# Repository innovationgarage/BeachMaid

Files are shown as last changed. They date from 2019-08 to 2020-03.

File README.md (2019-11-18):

# ePiMP
Electric Powered Intelligent Multipurpose Platform



In short, the ePiMP is a low cost, open source wooden tank robot, that can be constructed by a single sheet of 12 mm plywood, two cheap battery powered drills and few 3d printed parts.

## Changelog

* 2019-09-16: Version 1.1
   - Handles and holes to the backcover
   - Battery measurement circuit
   - Replaced wooden drive gears by plastic ones
   - 2 new mounting holes in the "lip" parts
* 2019-06-31: First version

## Fabrication

### Wooden pieces
All the pieces fit in a standard 2.44m by 1.2m sheet of plywood, 12 mm (15/32 in) thickness. The thickness can be changed but that would require changes in some internal slots that interlock, and some plastic pieces that assume 12 mm as the thickness.

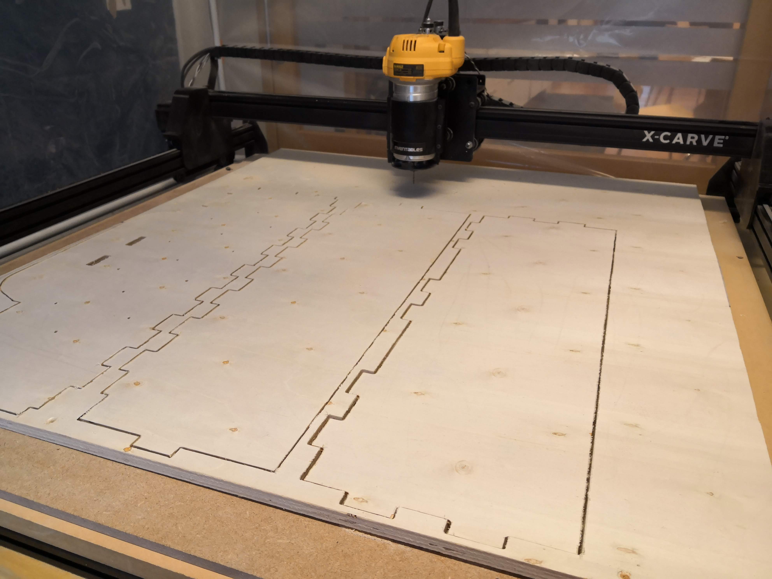
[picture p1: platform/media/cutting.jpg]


The list of parts wooden parts to cut in the CNC is aprox. 112 total pieces (depending on the version of the design)

#### Already layout sheets (for X-Carve 1000mm or similar)

The layout use 790mm square sheets:

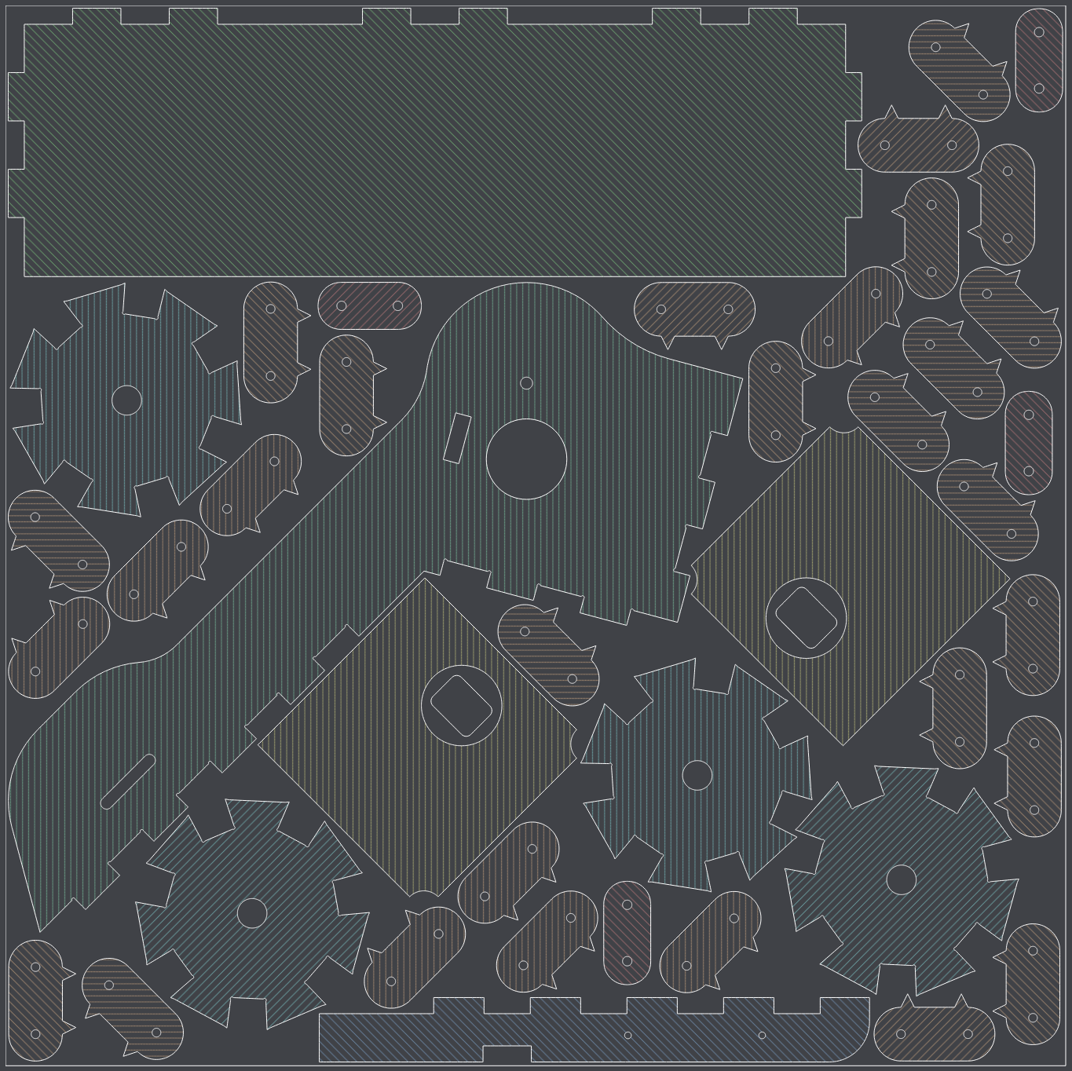
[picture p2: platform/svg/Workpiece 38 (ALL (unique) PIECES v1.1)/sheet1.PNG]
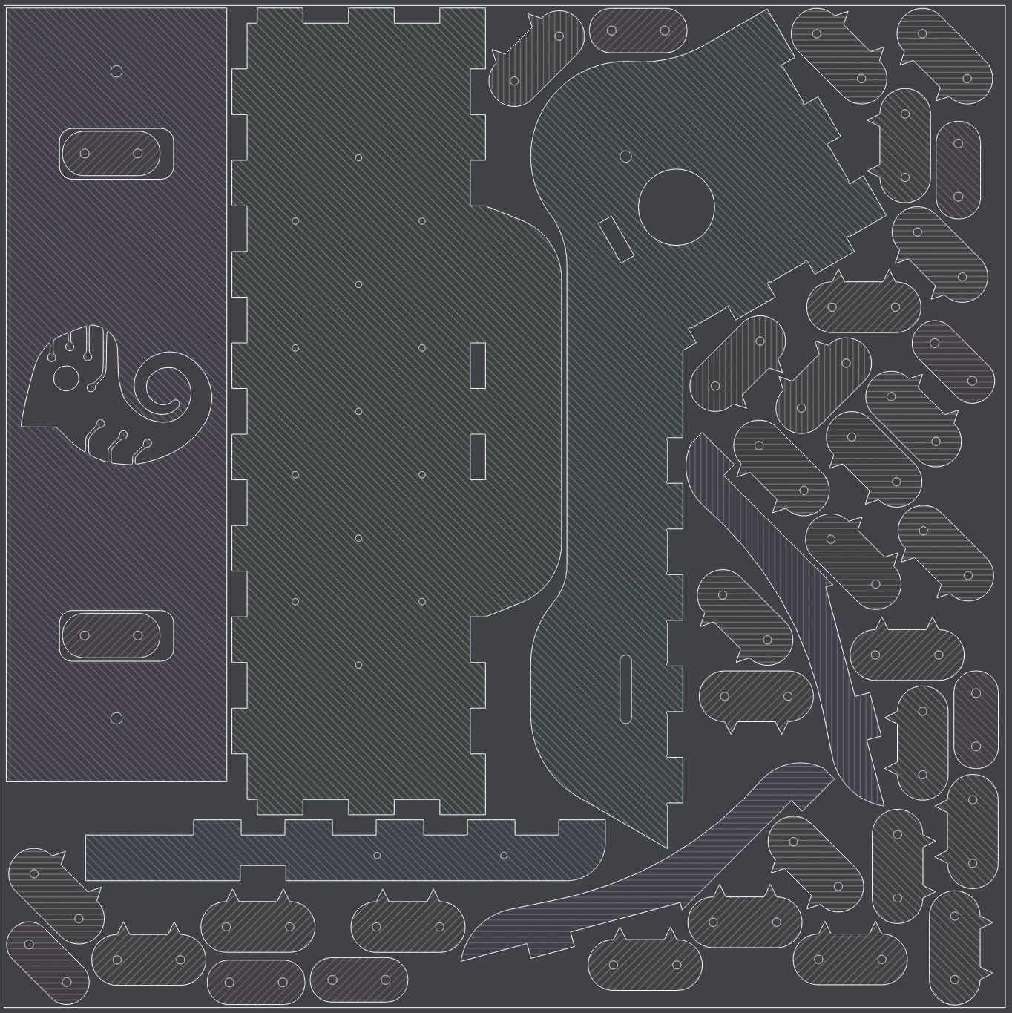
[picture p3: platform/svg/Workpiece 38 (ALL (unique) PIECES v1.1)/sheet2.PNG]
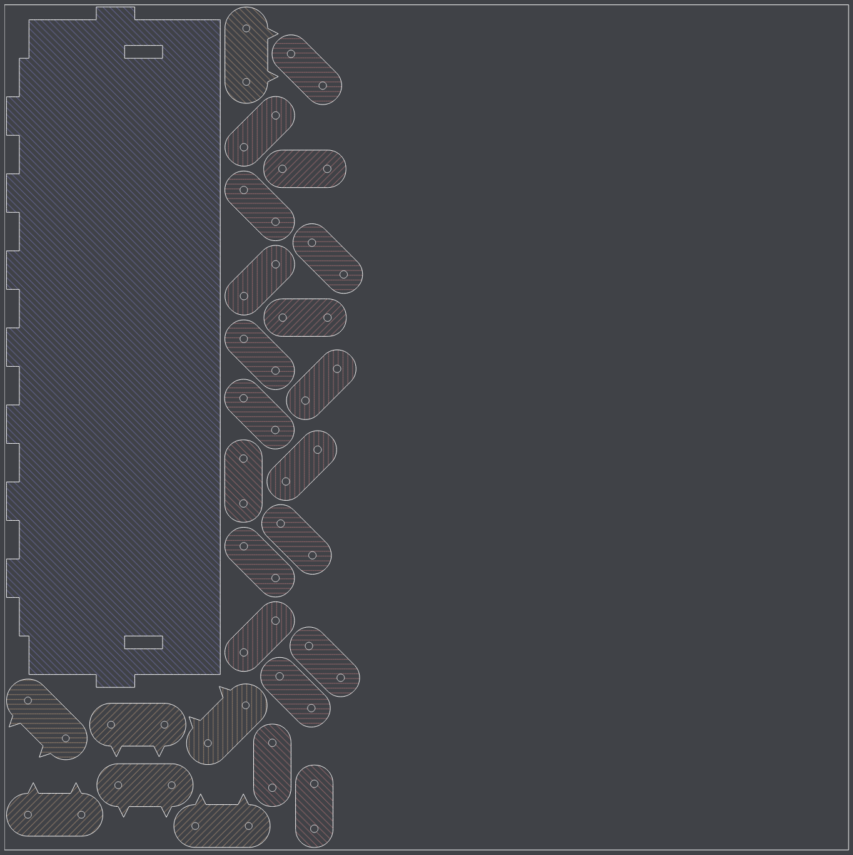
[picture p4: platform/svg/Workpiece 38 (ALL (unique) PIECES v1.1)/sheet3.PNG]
  

https://github.com/innovationgarage/epimp-body/blob/master/platform/svg/Workpiece%2038%20(ALL%20(unique)%20PIECES%20v1.1)/nested_optimized3.svg

#### Unique pieces

https://github.com/innovationgarage/epimp-body/blob/master/platform/svg/Workpiece%2038%20(ALL%20(unique)%20PIECES%20v1.1)/design.svg

The required quantity of the pieces is:

![](platform/svg/Workpiece%2038%20(ALL%20(unique)%20PIECES%20v1.1)/quantity.PNG)

### Plastic pieces
The list of needed printed parts is (56 total pieces, by the quantity specified in the filename):
https://github.com/innovationgarage/epimp-body/tree/master/platform/stl

## Assembly
You need the following parts and tools for the assembly:
* Wood glue
* Screwdrivers and wrenches
* 4x M8 long bolts (>10 cm) for the wheels
* 6x M8 inserts
* 2x M8 short bolts (>4 cm) for the back cover
* 2x M6 bolts and nut set for the clutch holder for the drills
* 2x cheap drills https://www.biltema.no/verktoy/el-verktoy/boremaskiner/drillskrutrekker-cd-12v-2000028475
* 8x skateboard ball bearings (608Z)
* 28x M6, 15 mm wood screws for the wheel center part that holds the bearings
* M5, 12 mm wood screws 
* M8 washers

### Wooden body

### Tank tracks
The tank tracks require 64x 6mm thick by 40 mm length wooden dowels https://www.aliexpress.com/item/32908209214.html. Before cutting the link pieces, test the fit of your dowels to ensure the friction between the outer parts is enough to hold everything without glue.

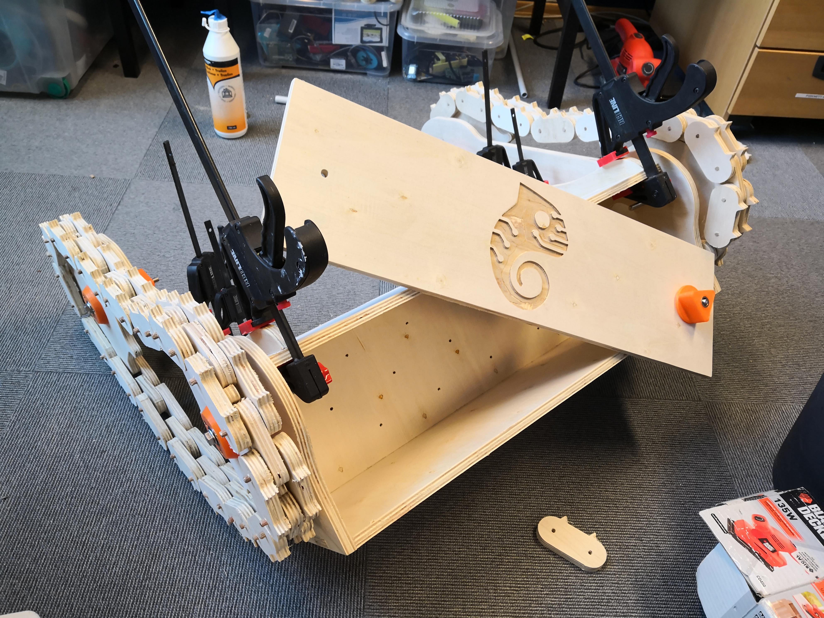
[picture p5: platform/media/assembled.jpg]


### Wheels and gears
The assembly is the following:

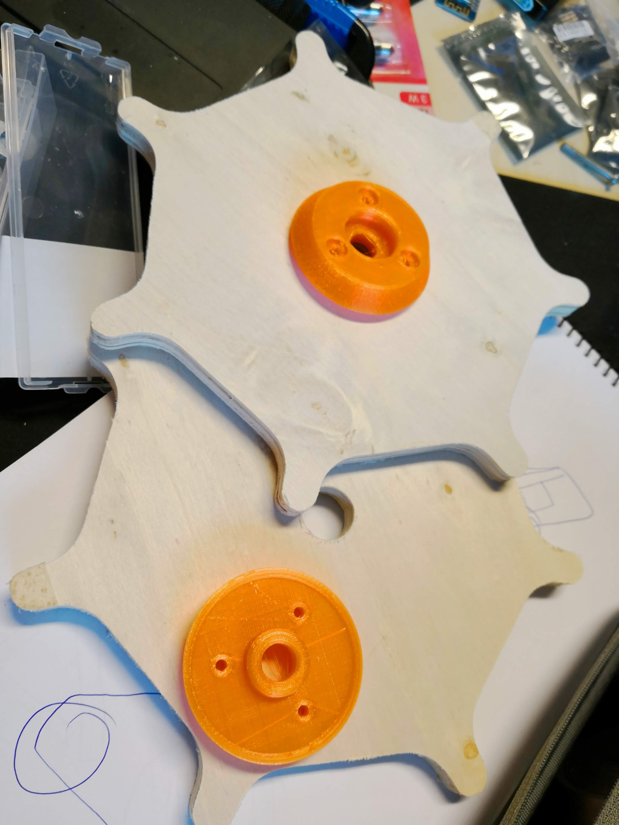
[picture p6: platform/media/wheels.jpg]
 

The wooden wheels go in between two bearing holders, using 3 of the M6 woodscrews per side. The two wheels on the back have the big gear in the interior side instead:

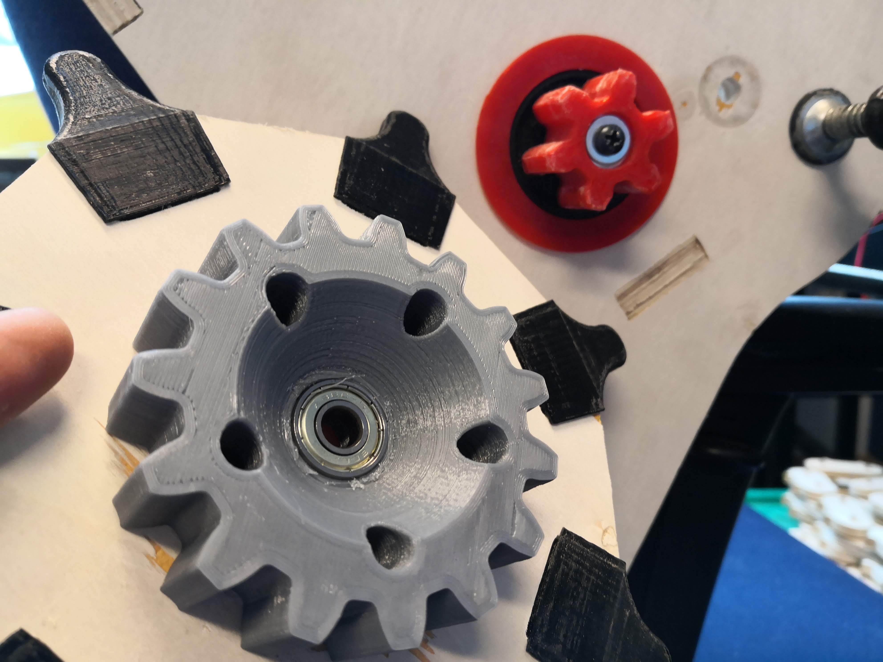
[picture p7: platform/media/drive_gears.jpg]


### Drive and electric system
The brain is a ESP8266 that allows you to remote control the robot via Blynk and serial. The following parts are required:
* ESP8266 board, like a Wemos D1
* 2x 43A motor controller https://www.amazon.com/HiLetgo-BTS7960-Driver-Arduino-Current/dp/B00WSN98DC
* 5V DC-DC board (LM2596 or similar, depicted as 7805 in the circuit below)
* Thick wire (14AWG or lower)
* Screw terminals for joining wire
* Some wire, resistors, switch, heat shrink, etc

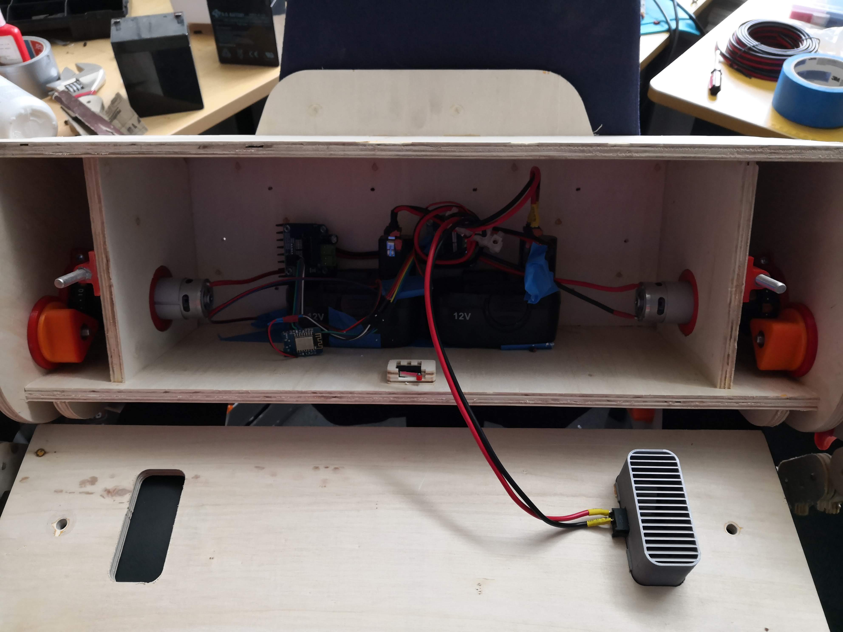
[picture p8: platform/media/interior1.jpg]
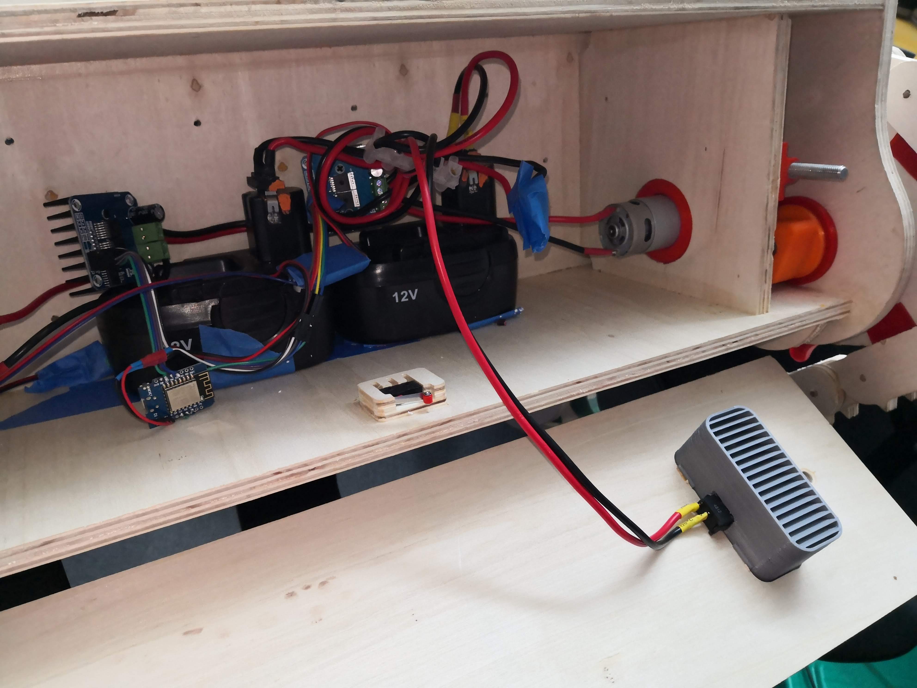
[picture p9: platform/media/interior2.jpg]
    

The resistor divider shown below is using 10K Ohm and 2.2K Ohm resistors for getting a value around 3V when the battery is fully charged. 
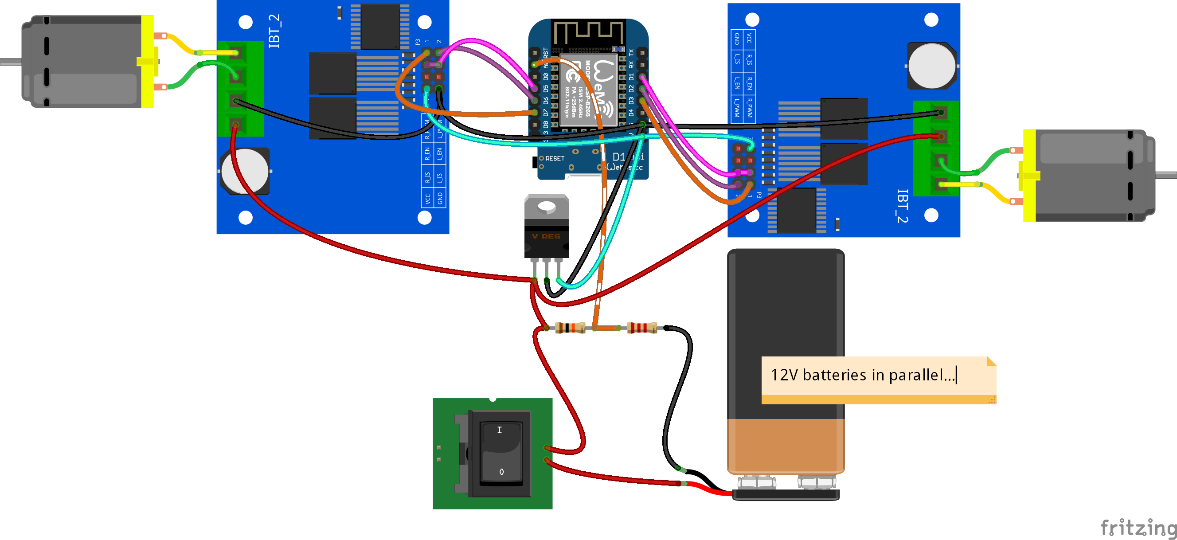
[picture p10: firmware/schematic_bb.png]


## Firmware

This is the firmware for the ESP8266: https://github.com/innovationgarage/epimp-body/tree/master/firmware/blynk_remote
QR code for cloning the Blynk app:

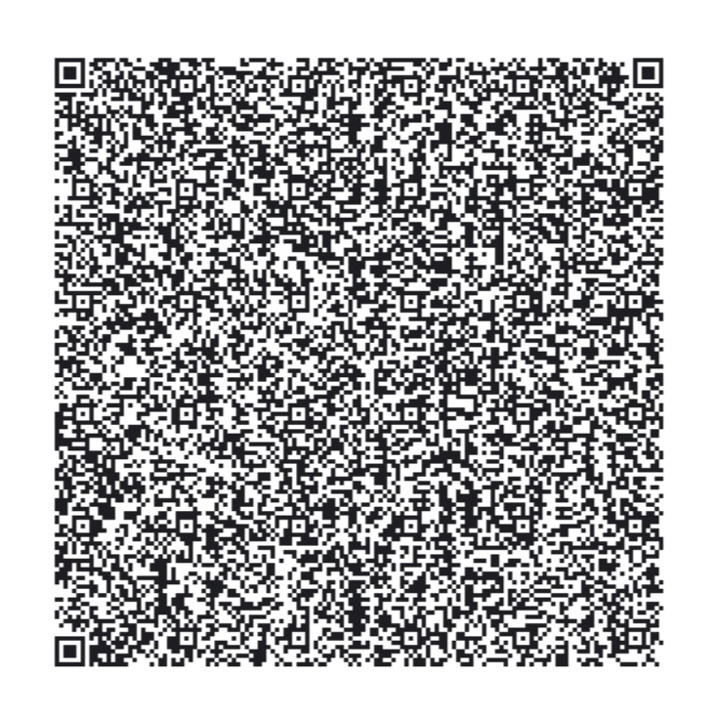
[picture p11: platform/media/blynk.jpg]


Remember to create a new Auth code, and fill the `credentials.h` file with your own information. Check https://github.com/innovationgarage/epimp-body/blob/master/firmware/README.md for more details about the firmware.

### Compile
For the compilation on Arduino you need the ESP8266 toolkit following: https://github.com/esp8266/Arduino#installing-with-boards-manager

Select "LOLIN(WEMOS) D1 R2 & Mini" from Tools/ Boards to compile.

Install the following libraries (Sketch/ Include library/ Manage):

* SimpleCLI
* Blynk

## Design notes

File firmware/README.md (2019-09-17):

## Serial CLI

The default is 8 data bits, no parity, one stop bit, bauds 115200.

    Innovation Garage AS - Woodynator-MK2 Build DATE TIME
    Available commands: 
    stop
    beep [-melody <0>]
    reboot [-force]
    help
    status [-stream] [-quiet]
    move -x <value> -y <value> [-smoothing <1>]
    belts -left <value> -right <value> [-smoothing <1>]

### Details

- `beep`: Melody number from https://github.com/innovationgarage/epimp-body/blob/master/firmware/blynk_remote/melody.ino

- `reboot`: `-force` triggers `ESP.reset()` instead of `ESP.restart()`

- `status`: `-stream` starts sending the current `millis()` and belt actual status via serial

- `move` and `belts`: `-smoothing` is the factor used here: https://github.com/innovationgarage/epimp-body/blob/master/firmware/blynk_remote/blynk_remote.ino#L127 in few words, if is 1 it will be a direct relationship. If is 2 it will be "half" of the setpoint every 100 ms, and so on

## Blynk

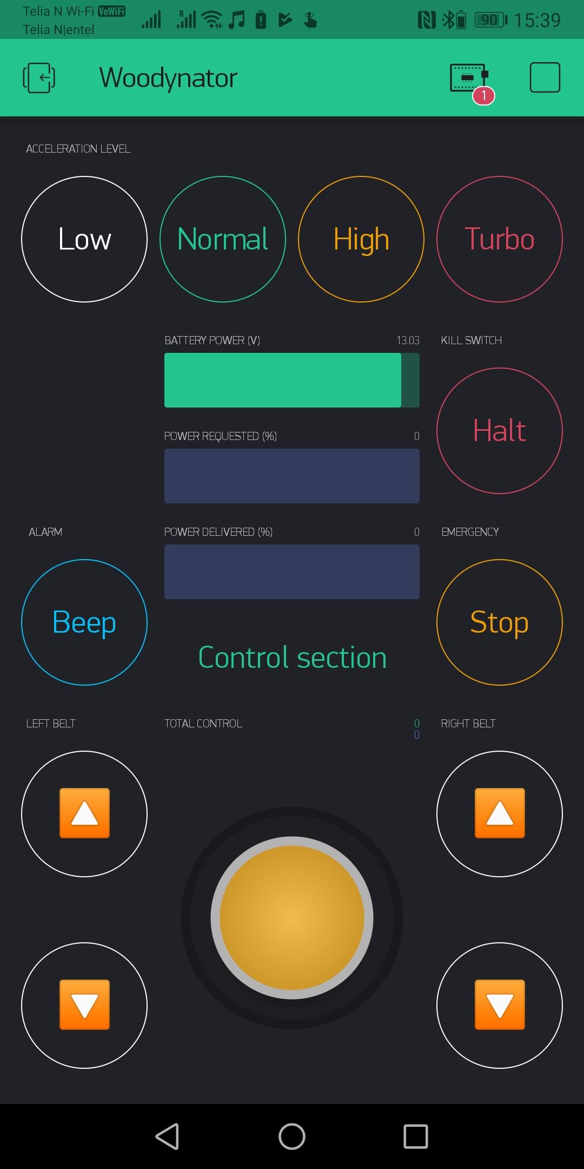
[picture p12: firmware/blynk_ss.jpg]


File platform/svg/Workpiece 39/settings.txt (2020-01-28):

Material type: Birch Plywood
Material dimensions: 760 mm x 760 mm x 12.5 mm
Bit: 2.3 mm, other-flat

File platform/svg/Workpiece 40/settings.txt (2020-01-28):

Material type: MDF
Material dimensions: 760 mm x 760 mm x 15.999999999999998 mm
Bit: 2.3 mm, other-flat

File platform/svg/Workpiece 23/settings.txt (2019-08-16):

Material type: Birch Plywood
Material dimensions: 590 mm x 150 mm x 12.5 mm
Bit: 2 mm, other-flat

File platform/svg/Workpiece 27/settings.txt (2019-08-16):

Material type: Birch Plywood
Material dimensions: 750 mm x 300 mm x 12 mm
Bit: 2 mm, other-flat

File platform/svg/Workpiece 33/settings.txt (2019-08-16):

Material type: Birch Plywood
Material dimensions: 750 mm x 300 mm x 12.5 mm
Bit: 2 mm, other-flat

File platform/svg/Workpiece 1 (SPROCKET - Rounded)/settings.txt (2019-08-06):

Material type: Birch Plywood
Material dimensions: 819.9999999999999 mm x 300 mm x 12 mm
Bit: 3 mm, other-flat

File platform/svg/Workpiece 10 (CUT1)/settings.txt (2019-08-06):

Material type: Birch Plywood
Material dimensions: 760 mm x 450 mm x 12.999999999999998 mm
Bit: 2 mm, other-flat

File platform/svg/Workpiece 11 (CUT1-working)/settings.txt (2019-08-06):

Material type: Birch Plywood
Material dimensions: 760 mm x 450 mm x 12.5 mm
Bit: 2 mm, other-flat

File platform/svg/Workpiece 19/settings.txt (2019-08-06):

Material type: Birch Plywood
Material dimensions: 760 mm x 319.99999999999994 mm x 12.5 mm
Bit: 2 mm, other-flat

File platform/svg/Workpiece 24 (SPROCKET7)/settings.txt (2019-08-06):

Material type: Birch Plywood
Material dimensions: 750 mm x 300 mm x 12.999999999999998 mm
Bit: 2 mm, other-flat

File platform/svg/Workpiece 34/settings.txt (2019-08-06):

Material type: Birch Plywood
Material dimensions: 760 mm x 739.9999999999999 mm x 12.5 mm
Bit: 2 mm, other-flat

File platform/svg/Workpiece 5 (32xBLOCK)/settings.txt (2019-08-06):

Material type: Birch Plywood
Material dimensions: 300 mm x 800 mm x 12.999999999999998 mm
Bit: 2 mm, other-flat

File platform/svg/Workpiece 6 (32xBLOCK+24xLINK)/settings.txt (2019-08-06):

Material type: Birch Plywood
Material dimensions: 300 mm x 750 mm x 12.5 mm
Bit: 2 mm, other-flat

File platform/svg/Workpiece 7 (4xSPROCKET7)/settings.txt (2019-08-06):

Material type: Birch Plywood
Material dimensions: 800 mm x 450 mm x 12.5 mm
Bit: 2 mm, other-flat

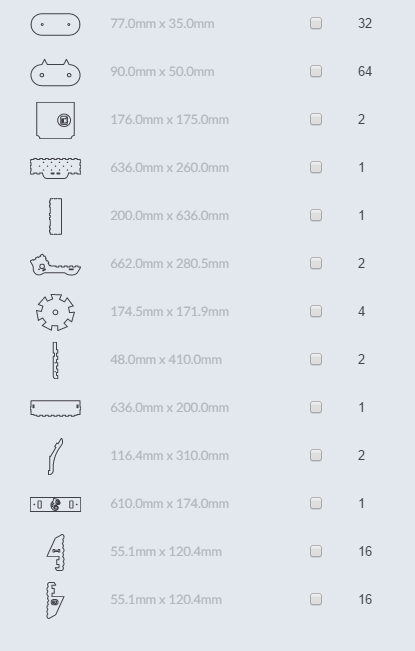
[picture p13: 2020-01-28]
platform/svg/Workpiece 41 (ALL (unique) PIECES v1.2)/quantity.PNG

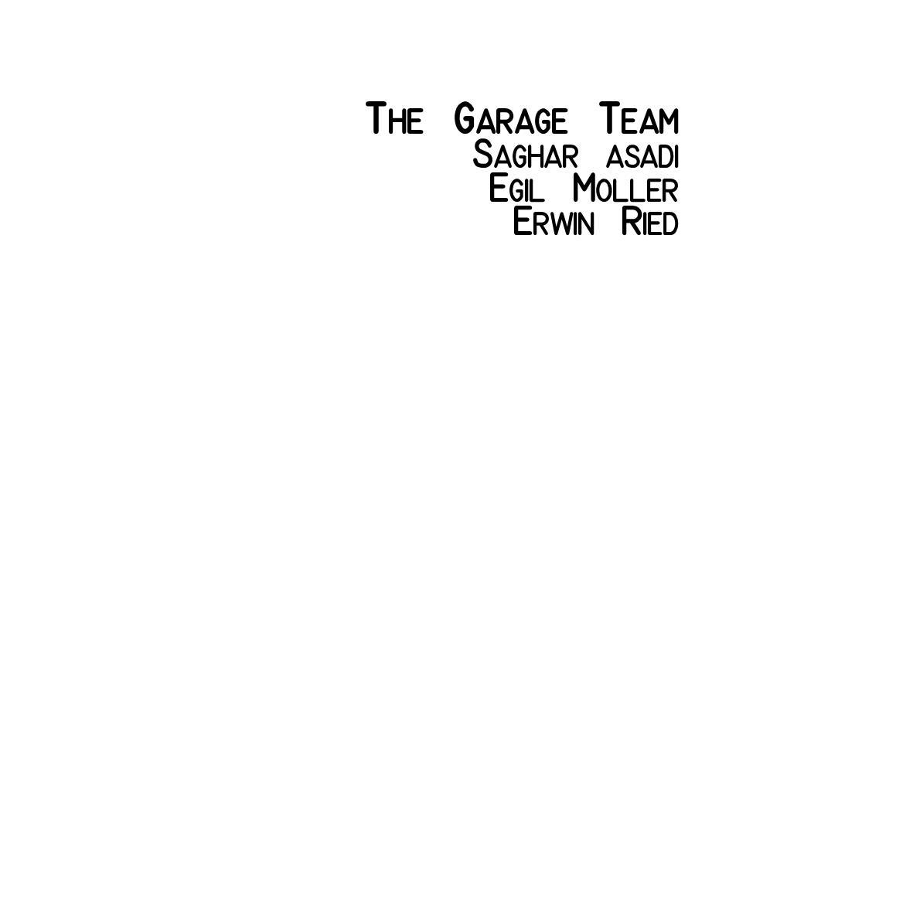
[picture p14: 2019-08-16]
platform/labels/labels.png

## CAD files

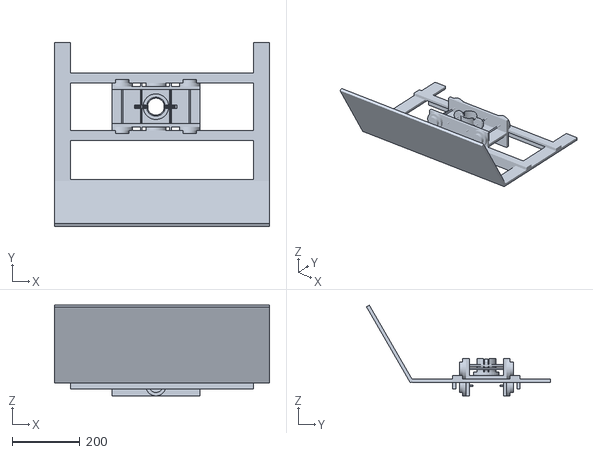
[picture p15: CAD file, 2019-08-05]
cart/cart.stl
636.0 x 544.8 x 268.4

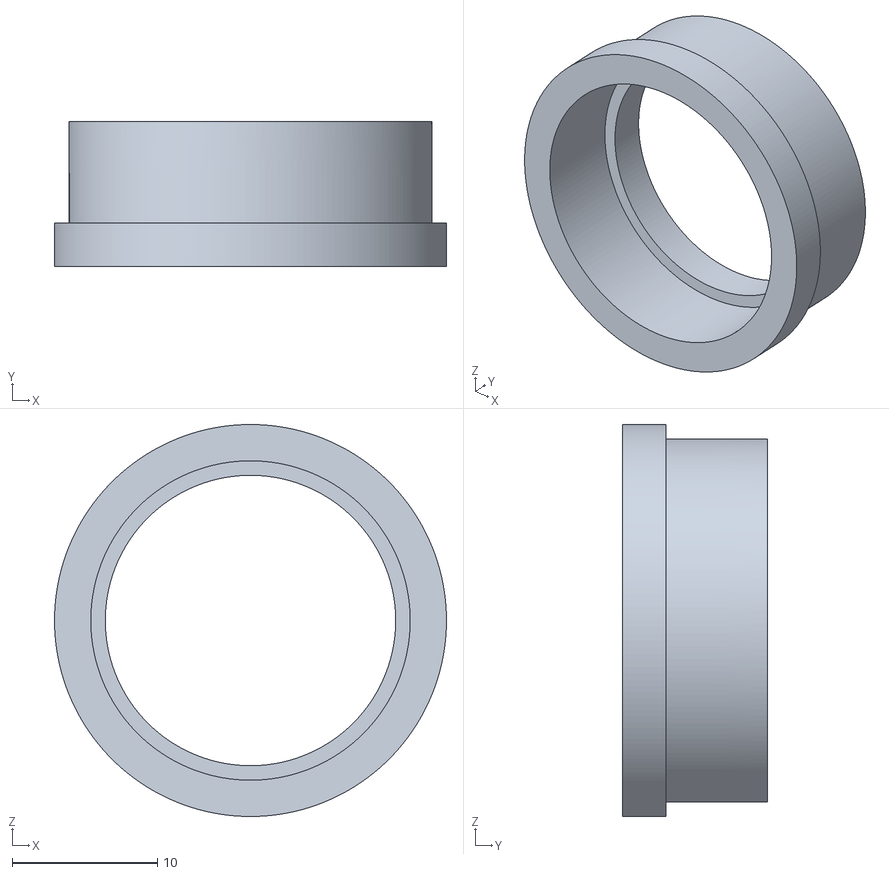
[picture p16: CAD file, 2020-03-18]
platform-2/9mm_lid/bearing_adapter_sleeve.stl
27.0 x 10.0 x 27.0

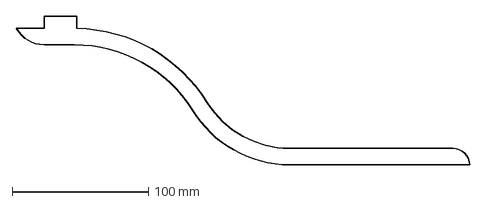
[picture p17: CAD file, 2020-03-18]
platform-2/9mm_lid/dxf/profile.dxf
332.3 x 108.9 mm

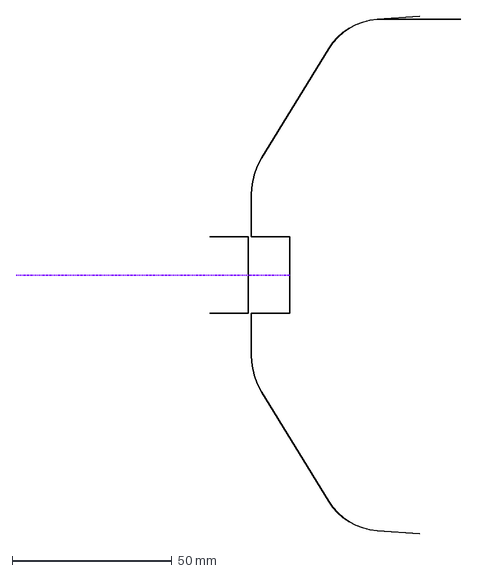
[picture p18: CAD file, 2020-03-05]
platform-2/dxf/correction.dxf
139.0 x 161.9 mm

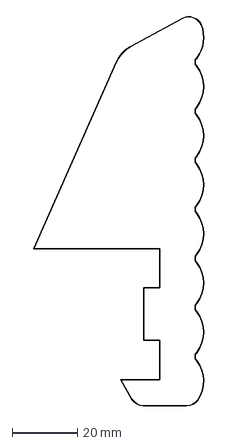
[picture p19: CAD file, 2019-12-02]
platform/dxf/snow_feet.dxf
52.6 x 119.0 mm

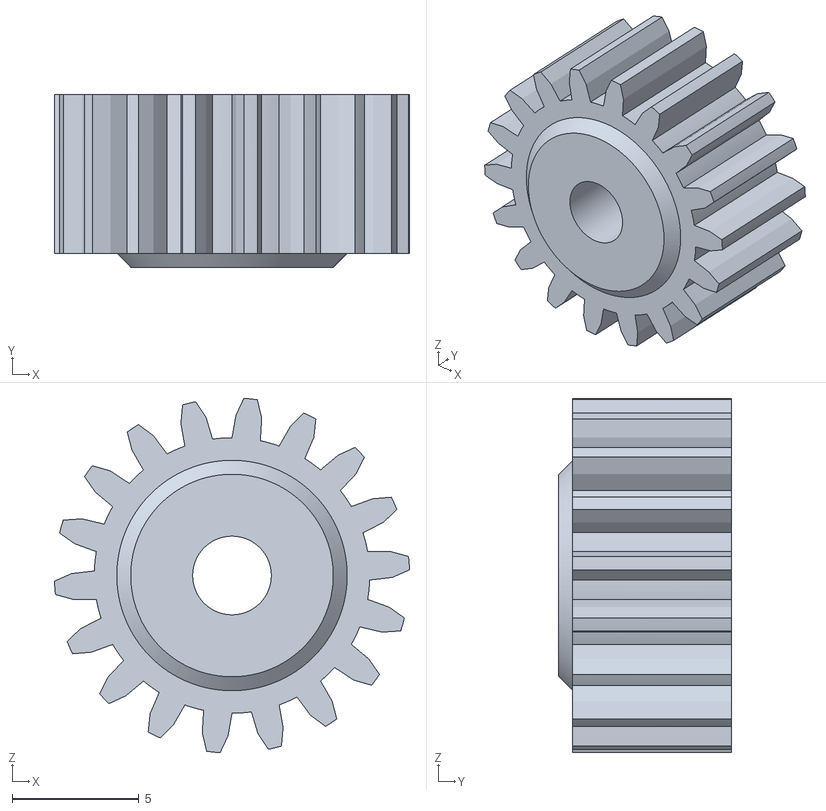
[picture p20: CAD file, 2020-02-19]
platform/metal_gearbox_gear.stl
14.0 x 6.80 x 14.0

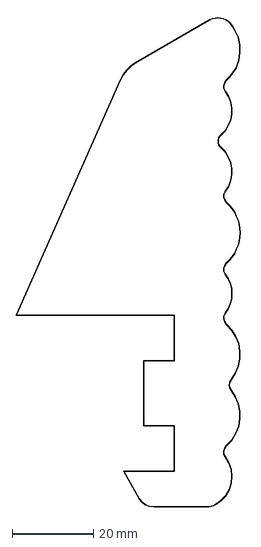
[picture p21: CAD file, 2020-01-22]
platform/snow_feet_letters/letter_i.dxf
56.2 x 120.8 mm

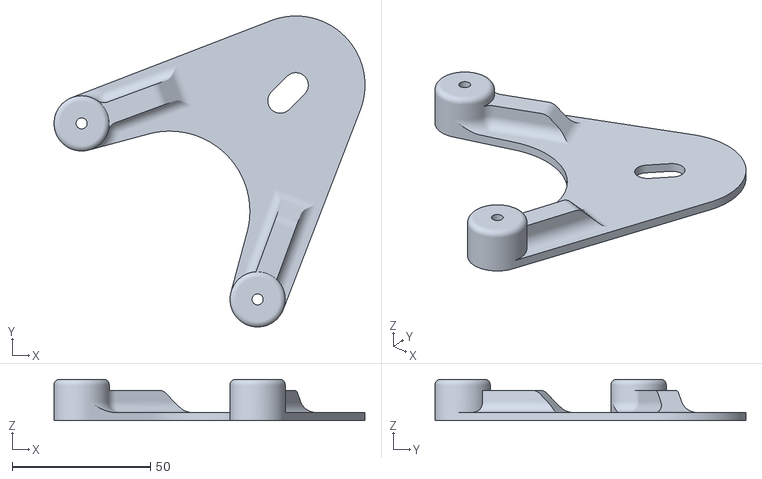
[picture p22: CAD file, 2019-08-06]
platform/stl/not_used/motor_tensioner.stl
112.5 x 112.5 x 15.0

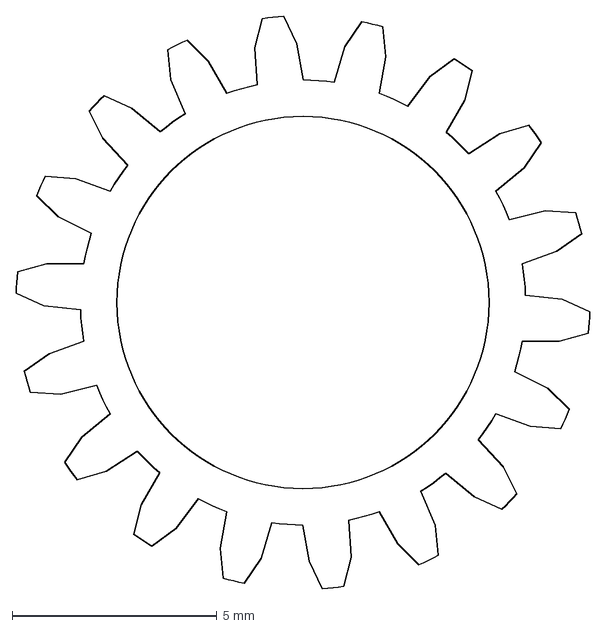
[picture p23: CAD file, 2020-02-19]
platform/svg/metal_gearbox_gear.dxf
14.0 x 14.0 mm

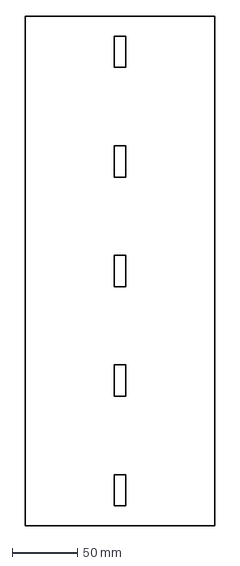
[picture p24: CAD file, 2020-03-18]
platform-2/9mm_lid/dxf/lid.dxf
145.0 x 390.0 mm

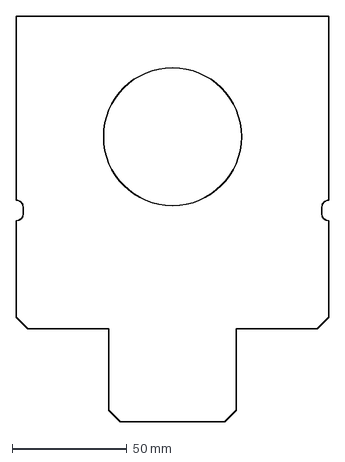
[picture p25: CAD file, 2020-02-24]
platform-2/dxf/middle.dxf
136.0 x 176.4 mm

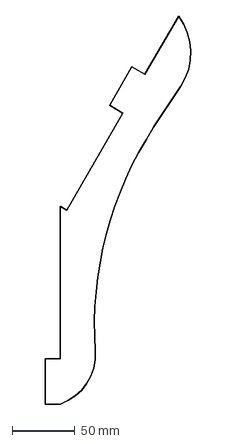
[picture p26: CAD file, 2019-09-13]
platform/dxf/stiffener.dxf
119.7 x 310.0 mm

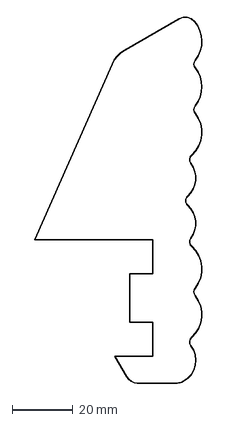
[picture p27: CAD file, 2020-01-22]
platform/snow_feet_letters/letter_g.dxf
56.2 x 120.8 mm

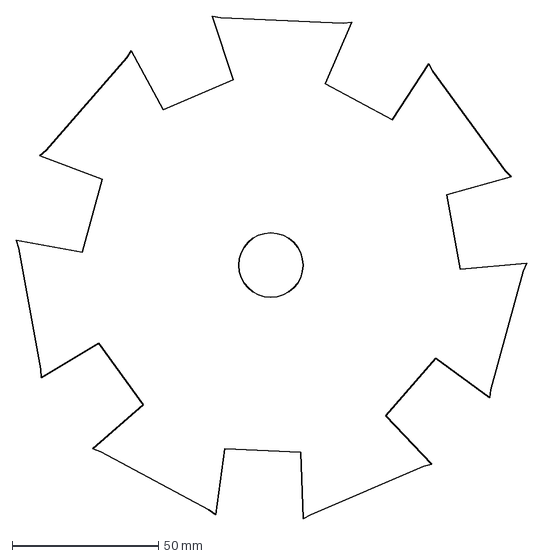
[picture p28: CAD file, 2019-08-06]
platform/sprocket7_mk2.dxf
174.5 x 171.9 mm

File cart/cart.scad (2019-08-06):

resolution=50;

platform_length=252.2;
platform_outer_length=260;
platform_width=636;
leg_length=410;
leg_width=48;
material=10;
plastic_material=3;

module wheel(r=60, pinr=2.5, thickness=10) {
    difference() {
        union() {
            cylinder(h=thickness, r=r, $fn=resolution);
            translate([0,0,thickness]) cylinder(h=thickness, r=r-thickness, $fn=resolution);
            }
        translate([0, 0, -thickness]) cylinder(h=thickness*4, r=pinr, $fn=resolution);
        }
    }

module cogwheel(r=40, h=material, cognr=10, cogr=50, pinr=2.5) {
    difference() {
        cylinder(r=r, h=h);
        for (pos = [0 : 360/cognr : 360]) {
            translate([cogr*cos(pos), cogr*sin(pos), -h]) cylinder(r=2*PI*cogr / cognr / 2, h=h*3);    
        }
        translate([0, 0, -h]) cylinder(h=h*3, r=pinr, $fn=resolution);
    }
}

module platform(platform_length=252.2, platform_outer_length=260, platform_width=636, leg_length=410, leg_width=48, material=10) {
    leg_spacing = platform_width - 2*leg_width;
    translate([0, 0, -material]) cube([leg_width, leg_length, material]);
    translate([leg_width+leg_spacing, 0, -material]) cube([leg_width, 410, material]);
    rotate(120, [1,0,0]) translate([0, -(platform_outer_length-platform_length), 0]) cube([platform_width, platform_outer_length, material]);
}

module track(gauge=140, width=30, height=30, platform_width=platform_width, leg_width=leg_width) {
    translate([0, -width, 0]) cube([platform_width, width, material]);
    translate([leg_width, -width, -height]) cube([platform_width-2*leg_width, material, height]);
    translate([0, gauge, 0]) cube([platform_width, width, material]);
    translate([leg_width, gauge+width-material, -height]) cube([platform_width-2*leg_width, material, height]);
}

module cart_wheels(radius=30, length=200, track_width=140, pinr=2.5) {
    translate([0,material,radius]) rotate(90, [1, 0, 0]) wheel(radius, pinr, material);
    translate([length,material,radius]) rotate(90, [1, 0, 0]) wheel(radius, pinr, material);
    translate([0,track_width-material,radius]) rotate(-90, [1, 0, 0]) wheel(radius, pinr, material);
    translate([length,track_width-material,radius]) rotate(-90, [1, 0, 0]) wheel(radius, pinr, material);
    
    translate([length/2,material,-radius+material]) rotate(90, [1, 0, 0]) wheel(radius, pinr, material);
    translate([length/2,track_width-material,-radius+material]) rotate(-90, [1, 0, 0]) wheel(radius, pinr, material);
}

module cart_boogie(radius=30, length=200, track_width=140, pinr=2.5) {
    cart_wheels(radius=radius, length=length, track_width=track_width, pinr=pinr);
    color([0, 0, 1]) translate([0, -material, radius]) rotate(-90, [1, 0, 0]) cylinder(r=pinr, h=track_width+2*material);
    color([0, 0, 1]) translate([length, -material, radius]) rotate(-90, [1, 0, 0]) cylinder(r=pinr, h=track_width+2*material);
    color([0, 0, 1]) difference() {
        translate([length/2, -material, -radius+material]) rotate(-90, [1, 0, 0]) cylinder(r=pinr, h=track_width+2*material);
        translate([length/2-2*pinr, 3*material, -radius+material-2*pinr]) cube([pinr*4, track_width-6*material, pinr*3]);
    }
}

module cart_base(wheel_radius=30, length=200, track_width=140, pipe_radius=25) {
    translate([-wheel_radius, material, 0])
        translate([0,material,0]) cube([length+2*wheel_radius, track_width-material*4, material]);
    translate([-wheel_radius, material, -2*wheel_radius+material]) cube([length+2*wheel_radius, material, wheel_radius*4-material]);
    translate([-wheel_radius, track_width-material-material, -2*wheel_radius+material]) cube([length+2*wheel_radius, material, wheel_radius*4-material]);
}

module sleeve(wheel_radius=wheel_radius, length=length, track_width=track_width, pipe_radius=pipe_radius) {
    translate([length/2, track_width/2, material]) difference() {
        union() {
          cylinder(r=pipe_radius+plastic_material, h=wheel_radius*2-material);
          cylinder(r=pipe_radius+plastic_material+material, h=material);
        }
        translate([0, 0, -1]) cylinder(r=pipe_radius, h=wheel_radius*2-material+2);
        translate([-pipe_radius-plastic_material-1,-material/2-plastic_material,material])
            cube([(pipe_radius+plastic_material)*2+2,material+2*plastic_material,wheel_radius*2-material+2]);
    }
}

module pipewheels(wheel_radius=30, length=200, track_width=140, pipe_radius=25, cogwheelr=20, pinr=2.5) {
    translate([length/2-pipe_radius-cogwheelr+2,track_width/2-material/2,2*wheel_radius-cogwheelr]) rotate(-90, [1,0,0]) cogwheel(r=cogwheelr, cogr=cogwheelr+2, cognr=20);
    translate([length/2+pipe_radius+cogwheelr-2,track_width/2-material/2,2*wheel_radius-cogwheelr]) rotate(-90, [1,0,0]) cogwheel(r=cogwheelr, cogr=cogwheelr+2, cognr=20);

    translate([length/2-pipe_radius-cogwheelr+2,0,2*wheel_radius-cogwheelr]) rotate(-90, [1, 0, 0]) cylinder(r=pinr, h=track_width);
    translate([length/2+pipe_radius+cogwheelr-2,0,2*wheel_radius-cogwheelr]) rotate(-90, [1, 0, 0]) cylinder(r=pinr, h=track_width);
}

module cart_base_w_holes(wheel_radius=30, length=200, track_width=140, pipe_radius=25, cogwheelr=20) {
    difference() {
        cart_base(wheel_radius=wheel_radius, length=length, track_width=track_width, pipe_radius=pipe_radius);
        cart_boogie(radius=wheel_radius, length=length, track_width=track_width, pinr=2.5);
        pipewheels(wheel_radius, length, track_width, pipe_radius, cogwheelr);
        translate([length/2, track_width/2, -material]) cylinder(r=pipe_radius, h=3*material);
    }
}

module cart(wheel_radius=30, length=200, track_width=140, pipe_radius=25, cogwheelr=20) {
    cart_base_w_holes(wheel_radius, length, track_width, pipe_radius, cogwheelr);
    color([.5, .5, 1]) sleeve(wheel_radius, length, track_width, pipe_radius);
    color([1,1,1]) pipewheels(wheel_radius, length, track_width, pipe_radius, cogwheelr);    
    cart_boogie(radius=wheel_radius, length=length, track_width=track_width, pinr=2.5);    
}


*color([1, 0, 0]) platform();
*translate([0,150,0]) track(width=30);
*translate([200,150,0]) cart();

translate([1000]) projection(cut=True) translate([0,0,-material]) rotate(90, [1, 0, 0]) cart_base_w_holes();

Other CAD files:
platform/drawings/mounting_points.dwg
platform/dxf/not_used/largegear.dxf
platform/dxf/not_used/gear_system.dxf
platform/stl/2x vent_cover.stl
platform-2/9mm_lid/OldVersions/assembly.0001.iam
platform-2/9mm_lid/OldVersions/middle.0001.ipt
platform-2/9mm_lid/OldVersions/profile_dock.0002.ipt
platform-2/9mm_lid/OldVersions/spray_holder_base.0001.ipt
platform-2/9mm_lid/arm.iam
platform-2/9mm_lid/arm.ipt
platform-2/9mm_lid/assembly.iam
platform-2/9mm_lid/bearing_adapter_sleeve.ipt
platform-2/9mm_lid/dxf/arm.dxf
platform-2/9mm_lid/dxf/base_arm.dxf
platform-2/9mm_lid/dxf/profile.dwg
platform-2/9mm_lid/lid.ipt
platform-2/9mm_lid/middle.ipt
platform-2/9mm_lid/profile_dock.ipt
platform-2/9mm_lid/spray_holder_base.ipt
platform-2/OldVersions/animation.0004.ipn
platform-2/OldVersions/body.0037.iam
platform-2/OldVersions/cover.0001.ipt
platform-2/OldVersions/internal.0009.ipt
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

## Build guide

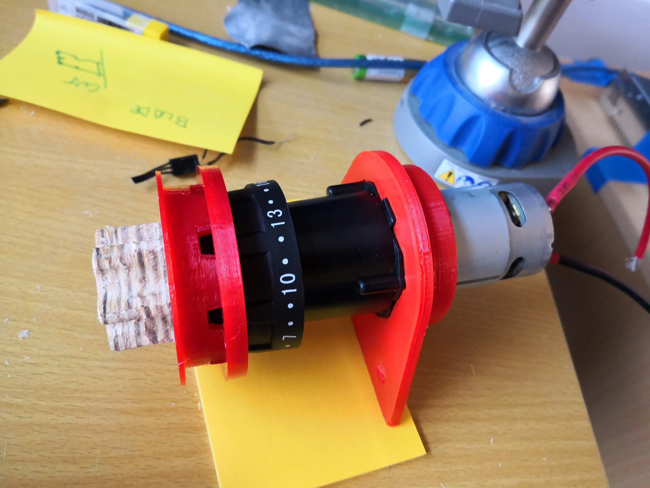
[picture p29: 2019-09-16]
platform/media/motor_assembly.jpg

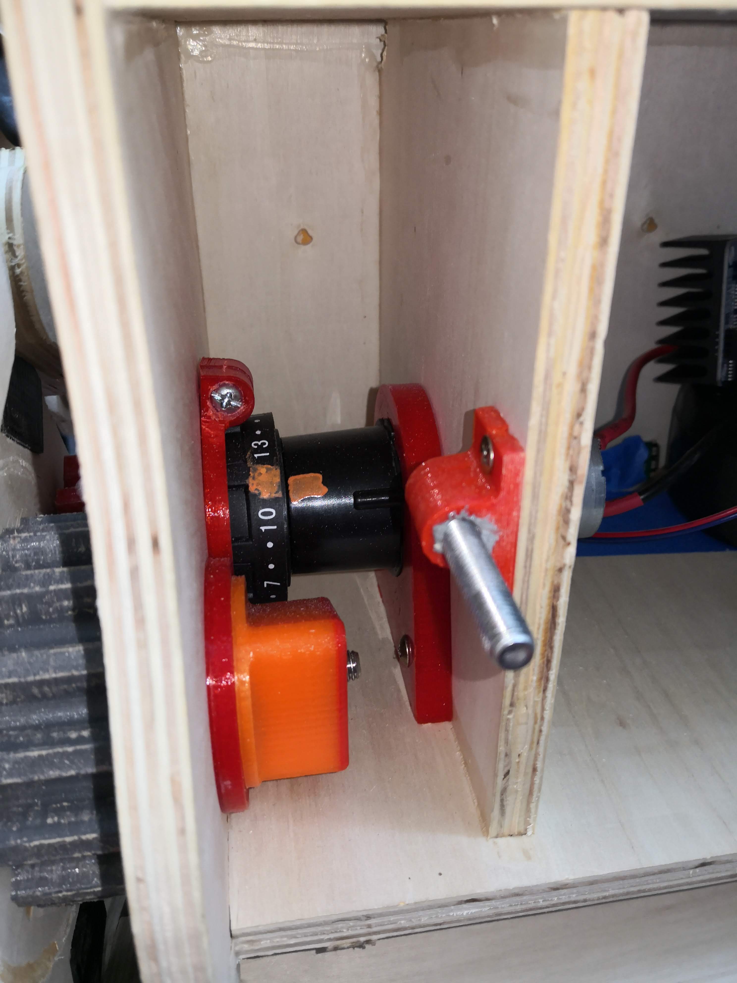
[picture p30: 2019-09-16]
platform/media/motor_assembly2.jpg

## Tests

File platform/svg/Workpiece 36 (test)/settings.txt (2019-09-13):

Material type: PCB
Material dimensions: 750 mm x 300 mm x 12.5 mm
Bit: 1.5 mm, other-flat

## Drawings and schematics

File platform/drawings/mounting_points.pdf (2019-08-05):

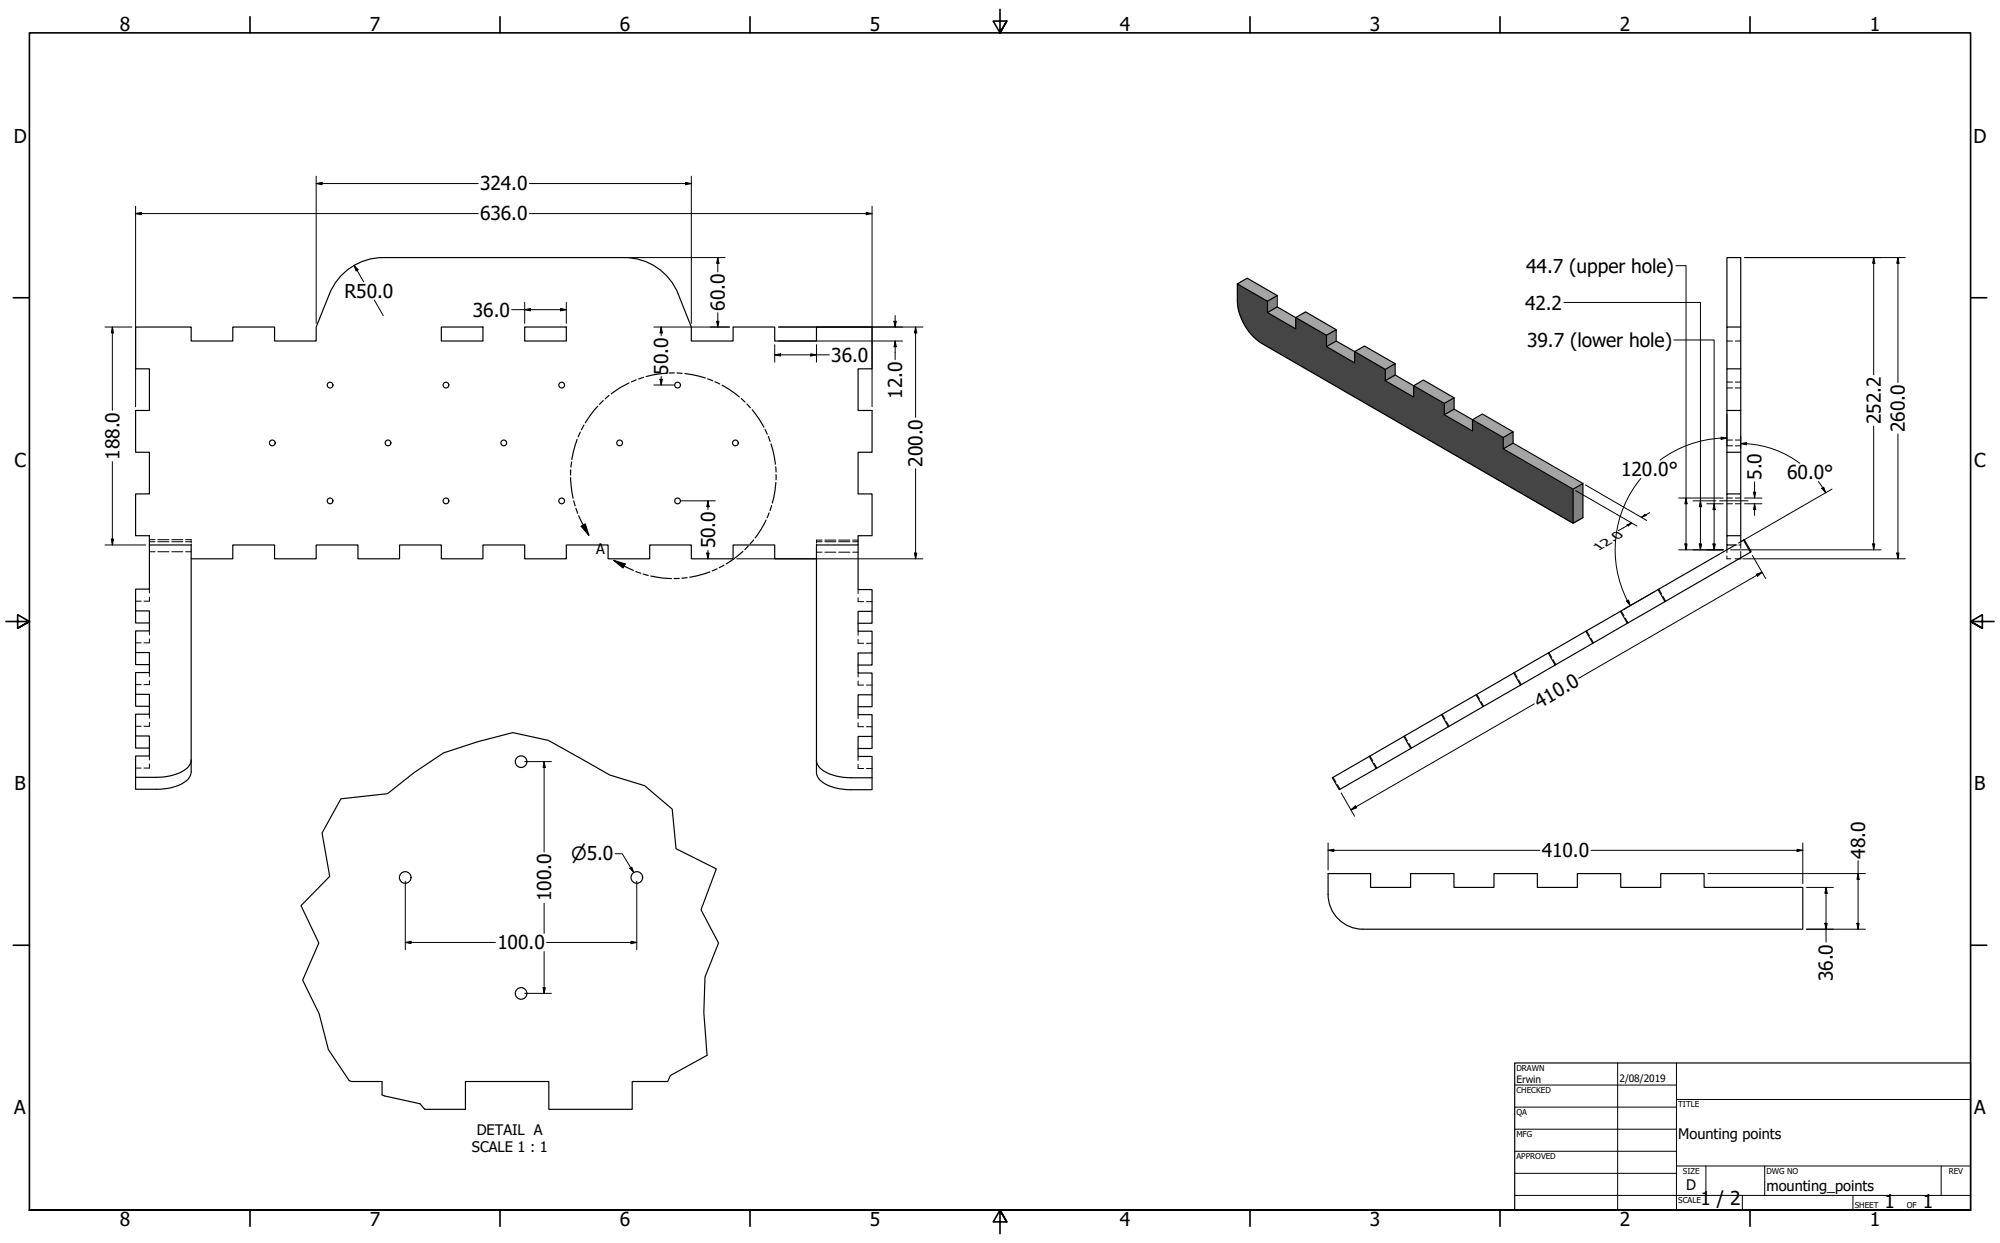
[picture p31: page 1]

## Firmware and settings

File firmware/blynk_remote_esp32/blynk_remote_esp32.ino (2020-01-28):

/* Comment this out to disable prints and save space */
#define BLYNK_PRINT Serial
//#define BLYNK_DEBUG // Optional, this enables more detailed prints

#include <SimpleCLI.h>
#include "credentials.h"
#include <WiFi.h>
#include <BlynkSimpleEsp32.h>
#include <WiFiMulti.h>
#include <analogWrite.h>

WiFiMulti wifiMulti;     // Create an instance of the ESP8266WiFiMulti class, called 'wifiMulti'
BlynkTimer speed_controller, system_status, remote_receiver;

// Motor pins
struct MotorPins
{
  byte RPWM;
  byte LPWM;
  byte L_R_EN;
};

// PINS
const byte battery_level_pin = 34;
const byte pwm_left_pin = 19, pwm_right_pin = 23;
const MotorPins rightEngine = { 13, 32, 33}, leftEngine = { 25, 26, 27};

int remote_x = 0, remote_y = 0;
unsigned long remote_stop = 0;
unsigned long noMessagesTimeout = 0;
const unsigned long stopAfterNoMessageMs = 4000;
float smoothing = 1, leftbelt_current = 0, rightbelt_current = 0;
int leftbelt_setpoint = 0, rightbelt_setpoint = 0;
boolean stop_all_signals_to_motors = false, offline_mode = false, verbose = false;

void setMotorSpeed(MotorPins motor, int speed, bool reverse = false)
{
  if (stop_all_signals_to_motors)
    return;

  speed *= reverse ? 1 : -1;
  int pwm = max(0, min(1024, (int)map(abs(speed), 0, 100, 0, 1024)));
  bool direction = speed > 0;

  if (pwm == 0)
  {
    // Electronic break
    digitalWrite(motor.RPWM, LOW);
    digitalWrite(motor.LPWM, LOW);
  }
  else
  {
    digitalWrite(motor.RPWM, direction);
    digitalWrite(motor.LPWM, !direction);
  }

  analogWrite(motor.L_R_EN, pwm);
}

void there_is_activity()
{
  noMessagesTimeout = millis() + stopAfterNoMessageMs;
}

void setBothMotorsSpeed(int left, int right)
{
  there_is_activity();
  leftbelt_setpoint = left;
  rightbelt_setpoint = right;
  check_and_set_speed();
}

void setMotorsDirection(int x, int y)
{
  int left, right;
  convertMotorsDirection(x, y, left, right);
  setBothMotorsSpeed(left, right);
}

void convertMotorsDirection(int x, int y, int &left, int &right)
{
  // From http://home.kendra.com/mauser/Joystick.html
  double X = max(-100, min(100, -1 * x));
  double Y = max(-100, min(100, -1 * y));

  double V = (100 - abs(X)) * (Y / 100) + Y;
  double W = (100 - abs(Y)) * (X / 100) + X;

  left = (V + W) / 2;
  right = (V - W) / 2;
}

void stop_all()
{
  float old = smoothing;
  smoothing = 1;
  setBothMotorsSpeed(0, 0);
  smoothing = old;
}

// CLI interface
SimpleCLI cli;
Command moveCmd, beltsCmd, stopCmd, helpCmd, statusCmd, beepCmd, rebootCmd;

// Callback in case of an error
void errorCallback(cmd_error* e)
{
  CommandError cmdError(e); // Create wrapper object

  Serial.print("ERROR: ");
  Serial.println(cmdError.toString());

  if (cmdError.hasCommand()) {
    Serial.print("Did you mean \"");
    Serial.print(cmdError.getCommand().toString());
    Serial.println("\"?");
  }
}

void setMotorPins( MotorPins motor)
{
  pinMode(motor.RPWM, OUTPUT);
  pinMode(motor.LPWM, OUTPUT);
  pinMode(motor.L_R_EN, OUTPUT); // Only using one pin for both
}

void check_and_set_speed()
{
  leftbelt_current += (leftbelt_setpoint - leftbelt_current) / smoothing;
  rightbelt_current += (rightbelt_setpoint - rightbelt_current) / smoothing;

  // Just remove some noise
  if (abs(leftbelt_setpoint - leftbelt_current) < 10)
    leftbelt_current = leftbelt_setpoint;

  if (abs(rightbelt_setpoint - rightbelt_current) < 10)
    rightbelt_current = rightbelt_setpoint;

  setMotorSpeed(leftEngine, leftbelt_current, true);
  setMotorSpeed(rightEngine, rightbelt_current, false);

  if (verbose)
  {
    Serial.print("$status=");
    Serial.print(millis());
    Serial.print(",");
    Serial.print(leftbelt_current);
    Serial.print(",");
    Serial.println(rightbelt_current);
  }
}

void loop() {
  if (!offline_mode)
  {
    Blynk.run();

    // Report info back to the remote
    system_status.run();
  }

  // Receiver
  remote_receiver.run();

  // Control the engines
  speed_controller.run();

  if (Serial.available())
  {
    // Read out string from the serial monitor
    String input = Serial.readStringUntil('\n');

    // Parse the user input into the CLI
    cli.parse(input);
  }

  if (cli.errored())
  {
    CommandError cmdError = cli.getError();

    Serial.print("ERROR: ");
    Serial.println(cmdError.toString());

    if (cmdError.hasCommand()) {
      Serial.print("Did you mean \"");
      Serial.print(cmdError.getCommand().toString());
      Serial.println("\"?");
    }
  }

  if ( remote_stop > 0 && millis() > remote_stop)
  {
    remote_stop = 0;
    stop_all();
  }
  else if (millis() > noMessagesTimeout)
  {
    stop_all();

    there_is_activity();
    check_connection();
  }
}

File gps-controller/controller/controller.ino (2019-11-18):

/*
  FSWebServer - Example WebServer with SPIFFS backend for esp8266
  Copyright (c) 2015 Hristo Gochkov. All rights reserved.
  This file is part of the ESP8266WebServer library for Arduino environment.

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
  upload the contents of the data folder with MkSPIFFS Tool ("ESP8266 Sketch Data Upload" in Tools menu in Arduino IDE)
  or you can upload the contents of a folder if you CD in that folder and run the following command:
  for file in `\ls -A1`; do curl -F "file=@$PWD/$file" esp8266fs.local/edit; done

  access the sample web page at http://esp8266fs.local
  edit the page by going to http://esp8266fs.local/edit
*/
#include <ESP8266WiFi.h>
#include <WiFiClient.h>
#include <ESP8266WebServer.h>
//#include <ESP8266mDNS.h>
#include <FS.h>

#define DBG_OUTPUT_PORT Serial

#ifndef APSSID
#define APSSID "GPS-Control"
//#define APPSK  "thereisnospoon"
#endif

/* Set these to your desired credentials. */
const char *ssid = APSSID;
//const char *password = APPSK;

const char* host = "esp8266fs";

ESP8266WebServer server(80);
//holds the current upload
File fsUploadFile;

//format bytes
String formatBytes(size_t bytes) {
  if (bytes < 1024) {
    return String(bytes) + "B";
  } else if (bytes < (1024 * 1024)) {
    return String(bytes / 1024.0) + "KB";
  } else if (bytes < (1024 * 1024 * 1024)) {
    return String(bytes / 1024.0 / 1024.0) + "MB";
  } else {
    return String(bytes / 1024.0 / 1024.0 / 1024.0) + "GB";
  }
}

String getContentType(String filename) {
  if (server.hasArg("download")) {
    return "application/octet-stream";
  } else if (filename.endsWith(".htm")) {
    return "text/html";
  } else if (filename.endsWith(".html")) {
    return "text/html";
  } else if (filename.endsWith(".css")) {
    return "text/css";
  } else if (filename.endsWith(".js")) {
    return "application/javascript";
  } else if (filename.endsWith(".png")) {
    return "image/png";
  } else if (filename.endsWith(".gif")) {
    return "image/gif";
  } else if (filename.endsWith(".jpg")) {
    return "image/jpeg";
  } else if (filename.endsWith(".ico")) {
    return "image/x-icon";
  } else if (filename.endsWith(".xml")) {
    return "text/xml";
  } else if (filename.endsWith(".pdf")) {
    return "application/x-pdf";
  } else if (filename.endsWith(".zip")) {
    return "application/x-zip";
  } else if (filename.endsWith(".gz")) {
    return "application/x-gzip";
  }
  return "text/plain";
}

bool handleFileRead(String path) {
  DBG_OUTPUT_PORT.println("handleFileRead: " + path);
  if (path.endsWith("/")) {
    path += "index.htm";
  }
  String contentType = getContentType(path);
  String pathWithGz = path + ".gz";
  if (SPIFFS.exists(pathWithGz) || SPIFFS.exists(path)) {
    if (SPIFFS.exists(pathWithGz)) {
      path += ".gz";
    }
    File file = SPIFFS.open(path, "r");
    server.streamFile(file, contentType);
    file.close();
    return true;
  }
  return false;
}

void handleFileUpload() {
  if (server.uri() != "/edit") {
    return;
  }
  HTTPUpload& upload = server.upload();
  if (upload.status == UPLOAD_FILE_START) {
    String filename = upload.filename;
    if (!filename.startsWith("/")) {
      filename = "/" + filename;
    }
    DBG_OUTPUT_PORT.print("handleFileUpload Name: "); DBG_OUTPUT_PORT.println(filename);
    fsUploadFile = SPIFFS.open(filename, "w");
    filename = String();
  } else if (upload.status == UPLOAD_FILE_WRITE) {
    //DBG_OUTPUT_PORT.print("handleFileUpload Data: "); DBG_OUTPUT_PORT.println(upload.currentSize);
    if (fsUploadFile) {
      fsUploadFile.write(upload.buf, upload.currentSize);
    }
  } else if (upload.status == UPLOAD_FILE_END) {
    if (fsUploadFile) {
      fsUploadFile.close();
    }
    DBG_OUTPUT_PORT.print("handleFileUpload Size: "); DBG_OUTPUT_PORT.println(upload.totalSize);
  }
}

void handleFileDelete() {
  if (server.args() == 0) {
    return server.send(500, "text/plain", "BAD ARGS");
  }
  String path = server.arg(0);
  DBG_OUTPUT_PORT.println("handleFileDelete: " + path);
  if (path == "/") {
    return server.send(500, "text/plain", "BAD PATH");
  }
  if (!SPIFFS.exists(path)) {
    return server.send(404, "text/plain", "FileNotFound");
  }
  SPIFFS.remove(path);
  server.send(200, "text/plain", "");
  path = String();
}

void handleFileCreate() {
  if (server.args() == 0) {
    return server.send(500, "text/plain", "BAD ARGS");
  }
  String path = server.arg(0);
  DBG_OUTPUT_PORT.println("handleFileCreate: " + path);
  if (path == "/") {
    return server.send(500, "text/plain", "BAD PATH");
  }
  if (SPIFFS.exists(path)) {
    return server.send(500, "text/plain", "FILE EXISTS");
  }
  File file = SPIFFS.open(path, "w");
  if (file) {
    file.close();
  } else {
    return server.send(500, "text/plain", "CREATE FAILED");
  }
  server.send(200, "text/plain", "");
  path = String();
}

void handleFileList() {
  if (!server.hasArg("dir")) {
    server.send(500, "text/plain", "BAD ARGS");
    return;
  }

  String path = server.arg("dir");
  DBG_OUTPUT_PORT.println("handleFileList: " + path);
  Dir dir = SPIFFS.openDir(path);
  path = String();

  String output = "[";
  while (dir.next()) {
    File entry = dir.openFile("r");
    if (output != "[") {
      output += ',';
    }
    bool isDir = false;
    output += "{\"type\":\"";
    output += (isDir) ? "dir" : "file";
    output += "\",\"name\":\"";
    output += String(entry.name()).substring(1);
    output += "\"}";
    entry.close();
  }

  output += "]";
  server.send(200, "text/json", output);
}

void setup(void) {
  DBG_OUTPUT_PORT.begin(115200);
  DBG_OUTPUT_PORT.print("\n");
  DBG_OUTPUT_PORT.setDebugOutput(true);
  SPIFFS.begin();
  {
    Dir dir = SPIFFS.openDir("/");
    while (dir.next()) {
      String fileName = dir.fileName();
      size_t fileSize = dir.fileSize();
      DBG_OUTPUT_PORT.printf("FS File: %s, size: %s\n", fileName.c_str(), formatBytes(fileSize).c_str());
    }
    DBG_OUTPUT_PORT.printf("\n");
  }


  //WIFI INIT
  WiFi.softAP(ssid);
  //WiFi.softAP(ssid, password);

  IPAddress myIP = WiFi.softAPIP();
  Serial.print("AP IP address: ");
  Serial.println(myIP);
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

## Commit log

2019-07-24 Prototype 1
    [Assembly.0002.iam, Assembly.iam, bearing_holder.0004.ipt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]
2019-07-24 Wooden parts
    [side.dxf, wooden.0003.iam, wooden.iam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]
2019-07-25 Drawings of the pieces
    [back.dxf, bottom.dxf, lip.dxf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]
2019-07-25 New version
    [wooden.iam, wooden_assembly.0005.iam, wooden_assembly.iam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]
2019-07-26 With the stiffener and backcover
    [backcover.dxf, stiffener.dxf, wooden_assembly.0005.iam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]
2019-08-02 Mounting point drawing
    [mounting_points.dwg]
2019-08-02 Update drawing
    [mounting_points.0001.dwg, mounting_points.dwg]
2019-08-05 First stab at cart solution
    [cart.scad, cart.stl]
2019-08-06 Remote control sketch
    [motor_frontalholder.0004.ipt, motor_frontalholder_combo.0001.iam, motor_frontalholder_retainerscrew.0001.ipt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]
2019-08-06 New version with plastic improvements
    [backcover_clamp.0001.ipt, backcover_clamp.ipt, backcover_clamp.stl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]
2019-08-16 Improved design
    [bearing_holder_large_gear.0002.ipt, bearing_holder_large_gear.ipt, bearing_holder_large_gear.stl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]
2019-09-12 Timeout and brakes if no activity
2019-09-13 Beep and reboot commands
    [blynk_remote.ino, cli.ino, setup.ino]
2019-09-13 Updated 1.1 pieces
    [backcover.dxf, bottom.dxf, lip.dxf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]
2019-09-13 Organized printed parts
    [28x sprocket7_mk2_plastic_pin.stl, 2x backcover_clamp_NEW.stl, 2x bearing_holder_large_gear.stl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]
2019-09-16 Simple electric schema
    [schematic.fzz]
2019-11-18 Some tests
    [schematic.fzz]
2019-12-02 Test 1 of snow feets
    [snow_feet.dxf, snow_feets.0003.ipt, snow_feets.ipt]
2020-01-22 Snow "tyres"
    [letter_g.0002.ipt, letter_g.dxf, letter_g.ipt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]
2020-01-22 Labels for the wood case
2020-01-27 New firmware for ESP32 and remote control
2020-01-27 Plastic bushing
    [plastic_axis_washer.0005.ipt, plastic_axis_washer.ipt, plastic_axis_washer.stl]
2020-01-28 Battery level working again
2020-02-19 New generation body
    [NEW_BODY_SLIM.0001.iam, animation.0004.ipn, animation.ipn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]
2020-02-24 Small changes on size
    [body.0034.iam, body.0035.iam, body.iam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]
2020-03-05 New plastic washers
    [plastic_wheel_washer.ipt, plastic_wheel_washer.stl, plastic_wheel_washer_keyed.ipt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]
2020-03-05 Correction for the side with wrong bending K-Factor
    [correction.dxf, side.ipt]
2020-03-18 New lid and new accesory mount
    [arm.0001.ipt, arm.dxf, arm.iam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]
